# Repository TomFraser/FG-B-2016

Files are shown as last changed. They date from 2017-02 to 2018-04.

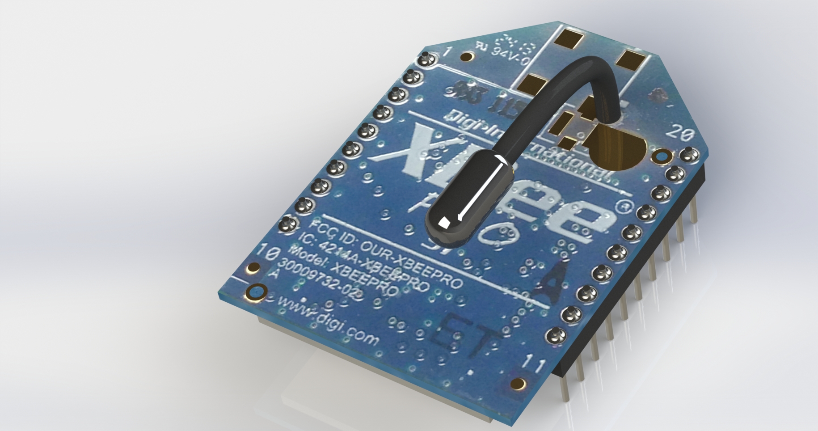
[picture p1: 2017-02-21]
design/components/xBee/Renderings/XBeeRender2.JPG

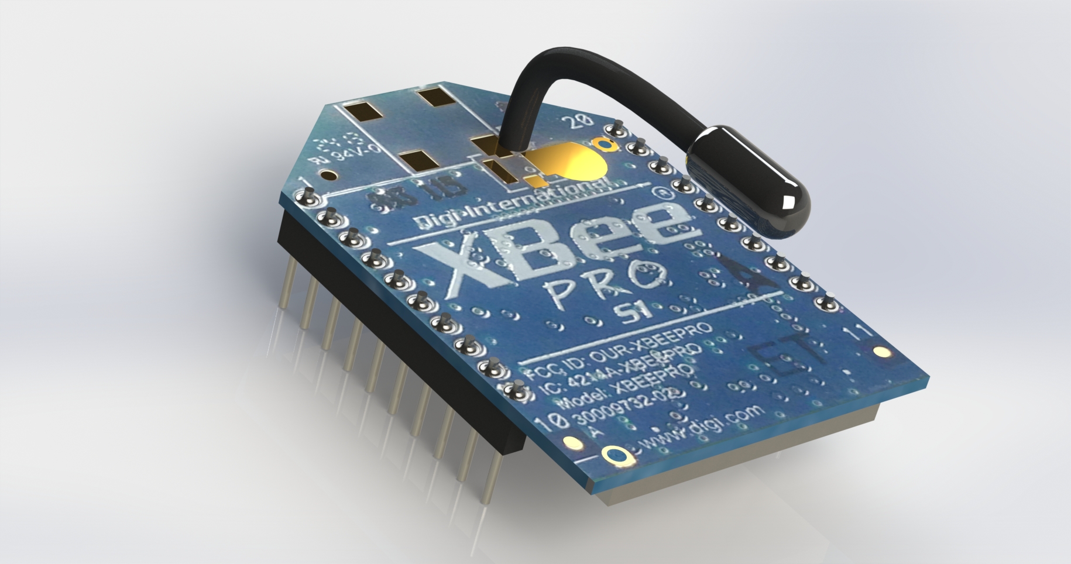
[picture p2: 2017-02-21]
design/components/xBee/Renderings/XBeeRender1.JPG

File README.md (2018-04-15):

# FG&B 2016 Repo
-------------------------------------------------------------

**Feel Free To Use Any Concepts Used Within This Repo.**
**If You Plan On Copying Large Parts Of Code, Please Email tr.fraser@bigpond.com For Permission**

-------------------------------------------------------------

**SHF Robotics**

Main Repo for FG&B Robotics (Formerly SHF Robotics) 2016

Tom Hulbert, Tom Fraser, Alistair English, William Plummer, Cooper Richmond :heart::heart:

-------------------------------------------------------------

To Do List
- [x] Make Robot
- [x] Make Robot Work
- [x] Watch Robot Fail at Nationals Because of the **curse**
- ^^^^ IT REALLY HAPPENED!

-------------------------------------------------------------

Sorry about rude commit messages, comments and messy code.

-------------------------------------------------------------

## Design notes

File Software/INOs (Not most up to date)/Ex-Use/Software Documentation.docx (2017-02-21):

5 Guys and a Box Robotics

Robot #2 Software Development Documentation

By Thomas Fraser

This documentation explains the ideas and methods used in the programming and design of Robot #2 for 5 Guys and a Box Robotics. The robot in question contains 3 Teensy 3.2 microcontrollers and multiple sensors. To learn more on the sensors used please refer to Hardware development documentation for Robot #2. Each Teensy is in charge of controlling certain sensors. The three Teensies communicate via SPI (Serial Peripheral Interface) to communicate.

Teensy 1:

Teensy one contains the lowest load during running with minimal tasks. Its primary task includes controlling the Serial Clock for the SPI communication, therefore it being the master in the SPI loop as well as communicating with the pixy and interfacing with the touch capacitive display.

Teensy 1 Software Design:

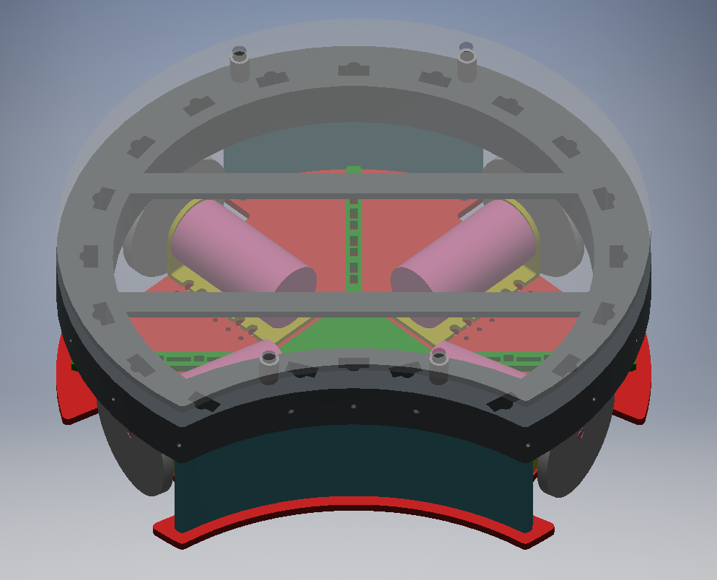
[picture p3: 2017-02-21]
images/renders/robot-front-angle.PNG

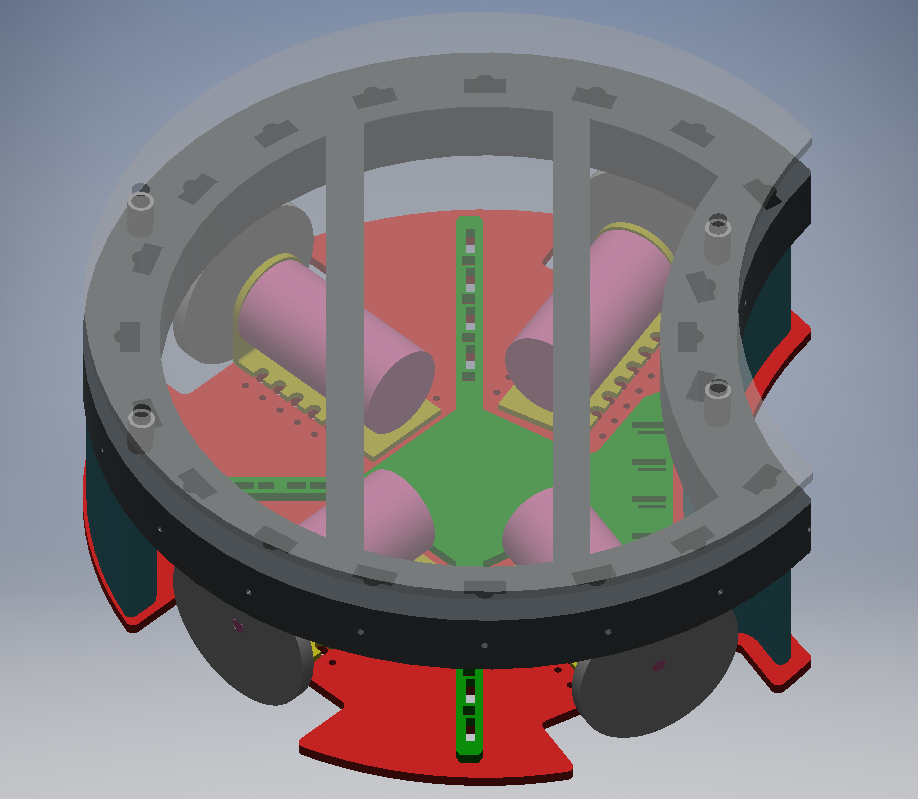
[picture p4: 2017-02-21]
images/renders/robot-side-angle.PNG

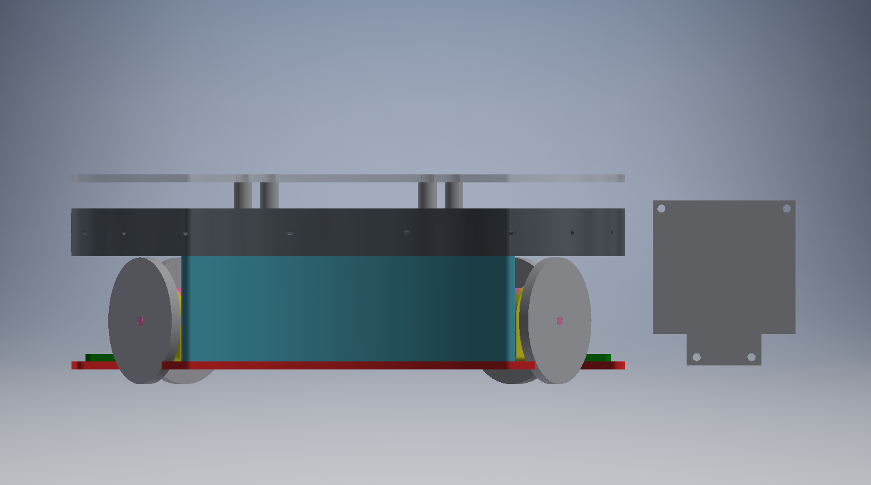
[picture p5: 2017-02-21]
images/renders/robot vs pixy.PNG

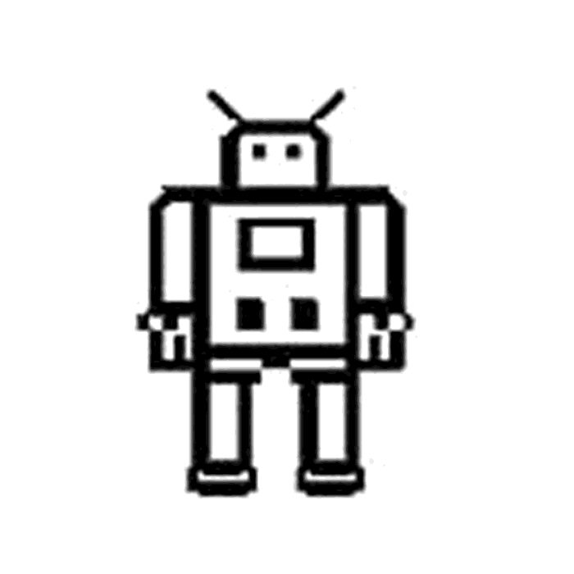
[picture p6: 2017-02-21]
images/stuff/robot.bmp

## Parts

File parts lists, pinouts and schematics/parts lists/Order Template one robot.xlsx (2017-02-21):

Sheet: ORDERS
Date Submitted | Team | Item | Description | Supplier | Vendor PN | Total QTY (inc. spares) | Spares | Price in original currency | Currency | Total price (AUD) | Link | Notes
2016-02-09 | SHF | LED | White L.E.D | Lighthouse LEDs |  | 25 |  | $0.26 | AUD | $6.50 | http://lighthouseleds.com/0805-smd-led-white-ultra-bright-340-mcd.html
2016-02-09 | SHF | LED | Red L.E.D | Lighthouse LEDs |  | 25 |  | $0.26 | AUD | $6.50 | http://lighthouseleds.com/0805-smd-led-red-ultra-bright-170-mcd.html
2016-02-09 | SHF | RES | 100 Ohm Resistor | Digi-Key |  | 50 |  | $0.06 | AUD | $2.94 | http://www.digikey.com.au/product-detail/en/CRCW0805100RJNEA/541-100ACT-ND/1180316
2016-02-09 | SHF | RES | 60 Ohm Resistor | Digi-Key |  | 25 |  | $0.14 | AUD | $3.50 | http://www.digikey.com.au/product-detail/en/RC0805FR-0760R4L/311-60.4CRCT-ND/731020
2016-02-09 | SHF | TRMPOT | Trim Pot 2k Ohm | Digi-Key |  | 5 |  | $1.48 | AUD | $7.40 | http://www.digikey.com.au/product-detail/en/3361P-1-202GLF/3361P-202GLFCT-ND/1089398
2016-02-09 | SHF | CAP | 100 (22) uF Cap | Digi-Key |  | 10 |  | $0.42 | AUD | $4.19 | http://www.digikey.com.au/product-detail/en/GRM21BR61E226ME44L/490-10749-1-ND/5251351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
2016-02-09 | SHF | CAP | 10 uF Cap | Digi-Key |  | 10 |  | $0.23 | AUD | $2.26 | http://www.digikey.com.au/product-detail/en/GRM21BR61E106KA73L/490-5523-1-ND/2334919
2016-02-09 | SHF | CAP | 1000uF Cap | Digi-Key |  | 10 |  | $0.92 | AUD | $9.20 | http://www.digikey.com.au/product-detail/en/UVR1V102MHD/493-1085-ND/588826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
2016-02-09 | SHF | VREG | 3.3v Vreg LM1084 | Digi-Key |  | 3 |  | $4.29 | AUD | $12.87 | http://www.digikey.com.au/product-detail/en/LM1084IS-3.3%2FNOPB/LM1084IS-3.3%2FNOPB-ND/363551
2016-02-09 | SHF | VREG | 5v Vreg LM1084 | Digi-Key |  | 3 |  | $4.29 | AUD | $12.87 | http://www.digikey.com.au/product-detail/en/LM1084IS-5.0%2FNOPB/LM1084IS-5.0%2FNOPB-ND/363552
2016-02-09 | SHF | OTHER | Screw Terminal 5mm (10pcs) | Digi-Key |  | 5 |  | $1.89 | AUD | $9.45 | http://www.ebay.com.au/itm/10Pcs-300V-2-Pin-Screw-Terminal-Block-Connector-5mm-Pitch-Panel-PCB-Mount-K2301-/351023553144
2016-02-09 | SHF | FUSE | Blade Fuse Holder | Digi-Key |  | 4 |  | $4.90 | AUD | $19.60 | http://www.digikey.com.au/product-detail/en/01530007Z/F064-ND/183333
2016-02-09 | SHF | FUSE | Blade Fuse 2 amp | Digi-Key |  | 5 |  | $1.52 | AUD | $7.60 | http://www.digikey.com.au/product-detail/en/BK%2FATM-2/283-2323-ND/264844
2016-02-09 | SHF | FUSE | Blade Fuses 7.5 amp | Digi-Key |  | 5 |  | $1.52 | AUD | $7.60 | http://www.digikey.com.au/product-detail/en/BK%2FATM-7-1%2F2/283-2327-ND/264851
2016-02-09 | SHF | JUMPR | JST Connectors | Digi-Key |  | 10 |  | $0.75 | AUD | $7.50 | http://www.digikey.com.au/product-detail/en/B2B-PH-SM4-TB(LF)(SN)/455-1734-1-ND/926831
2016-02-09 | SHF | JUMPR | JST Connector Receptical | Digi-Key |  | 15 |  | $0.14 | AUD | $2.10 | http://www.digikey.com.au/product-detail/en/PHR-2/455-1165-ND/608607
2016-02-09 | SHF | JUMPR | JST Crimp | Digi-Key |  | 25 |  | $0.14 | AUD | $3.50 | http://www.digikey.com.au/product-detail/en/SPH-002T-P0.5S/455-1127-1-ND/527358
2016-02-09 | SHF | JUMPR | 2x10 Shrouded Header Receptical | Ebay |  | 1 |  | $5.39 | AUD | $5.39 | http://www.ebay.com.au/itm/10-Pcs-2-54mm-2x10-Pin-20-Pin-Straight-Male-Shrouded-PCB-Box-header-IDC-Socket-/181148921363
2016-02-09 | SHF | JUMPR | 2x10 Shrouded Header Housing | Ebay |  | 1 |  | $7.10 | AUD | $7.10 | http://www.ebay.com.au/itm/10-Pcs-2-54mm-2x10-Pin-20-Pin-Male-Header-IDC-Ribbon-Cable-Transition-Connector-/171035372041
2016-02-09 | SHF | JUMPR | Ribbon Cable | Ebay |  | 1 |  | $13.86 | AUD | $13.86 | http://www.ebay.com.au/itm/6M-20-Pin-IDE-PATA-Extension-Flat-Ribbon-Cable-Wire-Gray-/331683344969
2016-02-09 | SHF | OTHER | Photo Transistor TEMT6000 | Allied Electronics |  | 25 |  | $0.63 | AUD | $15.75 | http://www.alliedelec.com/siliconix-vishay-temt6000x01/70026423/
2016-02-09 | SHF | OTHER | TSOPS | Tris10 |  | 0.5 |  | $60.00 | AUD | $30.00 | https://tris10.com/product/ir-sensor-50
2016-02-09 | SHF | MOTOR | Toshiba Motor Controller | Digi-Key |  | 5 |  | $3.72 | AUD | $18.60 | http://www.digikey.com.au/product-detail/en/TB6549PG(O)/TB6549PGO-ND/1730048
2016-02-09 | SHF | CAP | 0.22 uF Ceramic Cap | Digi-Key |  | 25 |  | $0.20 | AUD | $5.00 | http://www.digikey.com.au/product-detail/en/C0805C224K5RACTU/399-3491-1-ND/754784
2016-02-09 | SHF | CAP | 0.01 uF Ceramic (10000pF) Cap | Digi-Key |  | 25 |  | $0.05 | AUD | $1.24 | http://www.digikey.com.au/product-detail/en/GRM216R71H103KA01D/490-1664-1-ND/587472
2016-02-09 | SHF | CAP | 0.1 uF Ceramic Cap | Digi-Key |  | 25 |  | $0.03 | AUD | $0.78 | http://www.digikey.com.au/product-detail/en/CL21F104ZBCNNNC/1276-1007-1-ND/3889093
2016-02-09 | SHF | OTHER | Teensy 3.2 | OSHPark |  | 5 |  | $23.60 | AUD | $118.00 | http://store.oshpark.com/products/teensy-3-1
2016-02-09 | SHF | OTHER | BSS138 (Logic Level) | Digi-Key |  | 15 |  | $0.33 | AUD | $4.95 | http://www.digikey.com.au/product-detail/en/BSS138/BSS138CT-ND/244294
2016-02-09 | SHF | RES | 10k Ohm Resistor | Digi-Key |  | 100 |  | $0.01 | AUD | $1.04 | http://www.digikey.com.au/product-detail/en/RC0805JR-0710KL/311-10KARCT-ND/731188
2016-02-09 | SHF | OTHER | xBee Pro Series 2 | Little Bird |  | 0 |  | $36.65 | AUD | $0.00 | http://littlebirdelectronics.com.au/products/xbee-2mw-wire-antenna-series-2-zigbee-mesh
2016-02-09 | SHF | RES | 4.7k Ohm Resistor | Digi-Key |  | 30 |  | $0.14 | AUD | $4.20 | http://www.digikey.com.au/product-detail/en/RC0805FR-074K7L/311-4.70KCRCT-ND/730876
2016-02-09 | SHF | JUMPR | 2x3 Shrouded Header Receptical | Digi-Key |  | 10 |  | $0.66 | AUD | $6.62 | http://www.digikey.com/product-detail/en/75869-131LF/609-2845-ND/1302569
2016-02-09 | SHF | SENSOR | MPU 9250 | Little Bird |  | 5 |  | $2.92 | AUD | $14.60 | http://www.ebay.com.au/itm/New-SPI-IIC-MPU-9250-9-Axis-Attitude-Sensor-Module-Gyro-Accelerator-Magnetometer-/191152604672
2016-02-09 | SHF | SENSOR | Pixy | Tribotix |  | 1 |  | $70.00 | AUD | $70.00 | http://www.tribotix.com/Products/CharmedLabs/Pixy.htm
2016-02-09 | SHF | LIPO | 14.8v Lipo 1800mAh | Hobby King |  | 3 |  | $22.91 | AUD | $68.73 | http://www.hobbyking.com/hobbyking/store/uh_viewitem.asp?idproduct=24616
2016-02-09 | SHF | LIPO | Lipo Charger (for simultaneous charging) | Hobby King |  | 0 |  | $59.99 | AUD | $0.00 | http://www.hobbyking.com/hobbyking/store/__58285__IMAX_B6AC_V2_Professional_Balance_Charger_Discharger.html
2016-02-09 | SHF | LCD | LCD 2.8" Cap Touch | Adafruit |  | 1 |  | $55.00 | AUD | $55.00 | https://www.adafruit.com/products/2090
2016-02-09 | SHF | OTHER | Switch SPDT | Ali Express |  | 3 |  | $3.55 | AUD | $10.65 | http://www.aliexpress.com/item/SB-DC-12V-20A-Lgnition-LED-SPST-ON-OFF-Car-Toggle-Covered-Rocket-Missile-Switch-Red/32458116746.html
2016-02-09 | SHF | MOTOR | DIP 16 Socket | Digi-Key |  | 5 |  | $0.36 | AUD | $1.80 | http://www.digikey.com.au/product-detail/en/A16-LC-TT/AE9992-ND/821746
2016-02-09 | SHF | OTHER | Hookup Wire | Little Bird |  | 0 |  | $31.05 | AUD | $0.00 | http://littlebirdelectronics.com.au/products/hook-up-wire-spool-set-22awg-solid-core-6-x-25-ft
2016-02-09 | SHF | MOTOR | Motors 500RPM 12V DC | Polulu |  | 5 |  | $12.17 | AUD | $60.85 | http://www.aliexpress.com/item/DC-12V-500RPM-25GA-40mA-High-Torque-Electric-Gear-Box-Motor-25MM/32270478250.html
2016-02-09 | SHF | SOLDER | Solder Paste No Clean Lead-Free | Digi-Key |  | 1 |  | $21.73 | AUD | $21.73 | http://www.digikey.com.au/product-detail/en/SMD291SNL/SMD291SNL-ND/1160001
2016-02-09 | SHF | JUMPR | Male SMD Header 0.1" | Ebay |  | 2 |  | $7.09 | AUD | $14.18 | http://www.ebay.com.au/itm/10pcs-RoHS-2-54mm-Pitch-2X40-Pin-Header-Strip-Double-Row-SMT-SMD-Male-PCB-Board-/271556499758
2016-02-09 | SHF | JUMPR | Female Header 0.1" | Ebay |  | 5 |  | $1.60 | AUD | $8.00 | http://www.ebay.com.au/itm/10pcs-40-Way-Single-Female-HEADER-Connector-0-1-2-54mm-Breakable-Pin-For-PCB-/271841180849
2016-02-09 | SHF | SOLDER | Solder 0.51mm Lead-Free | Digi-Key |  | 0 |  | $30.89 | AUD | $0.00 | http://www.digikey.com.au/product-detail/en/SMDSWLF.020%204OZ/SMDSWLF.020%204OZ-ND/2177058
2016-02-09 | SHF | MOTOR | Dodgy Uranium (Iranium) Omni-Wheels | Alibaba |  | 5 |  | $17.50 | AUD | $87.50 | http://www.alibaba.com/product-detail/omni-directional-wheel_146767461.html
2016-02-09 | SHF | MOTOR | Motor Mounts | Polulu |  | 5 |  | $7.45 | AUD | $37.25 | https://www.pololu.com/product/2676
2016-02-09 | SHF | TRMPOT | Trim Pot 1k Ohm | Digi-Key |  | 10 |  | $1.48 | AUD | $14.80 | http://www.digikey.com.au/product-detail/en/3361P-1-102GLF/3361P-102GLFCT-ND/1089394
2016-02-09 | SHF | RES | 10 Ohm Resistor | Digi-Key |  | 100 |  | $0.01 | AUD | $1.21 | http://www.digikey.com.au/product-detail/en/RC0805FR-0710RL/311-10.0CRCT-ND/730481
2016-02-09 | SHF | JUMPR | XT60 Connector | Hobby King |  | 1 |  | $5.75 | AUD | $5.75 | http://www.hobbyking.com/hobbyking/store/uh_viewitem.asp?idproduct=43416
2016-02-09 | SHF | OTHER | Rocker Switch SPDT (4pcs) | Ebay |  | 3 |  | $1.82 | AUD | $5.46 | http://www.ebay.com.au/itm/4-Pcs-x-AC-250V-6A-125V-10A-on-on-SPDT-Boat-Rocker-Switch-3-Solder-Lug-Pin-Black-/391159131408
2016-02-09 | SHF | SENSOR | M12 130 degree Lense (pixy) | M12Lense.com |  | 1 |  | $9.98 | AUD | $9.98 | http://www.m12lenses.com/2-5mm-F2-5-Board-Lens-p/pt-02520.htm
2016-02-09 | SHF | OTHER | Adhesive Paper | Ebay |  | 1 |  | $2.00 | AUD | $2.00 | http://www.ebay.com.au/itm/20-sheets-A4-105GSM-Inkjet-and-laser-Matte-Label-Paper-Sticker-Adhesive-/181989139085
2016-02-09 | SHF | OTHER | PVC Sheet Grey (at least 1000*300mm) | Plastic Wholesale |  | N/A |  | N/A | AUD |  | http://www.plasticwholesale.com.au/
2016-02-09 | SHF | OTHER | PVC Sheet Clear (at least 1000*300mm) | Plastic Wholesale |  | N/A |  | N/A | AUD |  | http://www.plasticwholesale.com.au/
2016-02-09 | SHF | OTHER | Solid Core Wire 6x25ft | Little Bird |  | 1 |  | $31.00 | AUD | $31.00 | http://littlebirdelectronics.com.au/products/hook-up-wire-spool-set-22awg-solid-core-6-x-25-ft
2016-02-09 | SHF | OTHER | Heat Shrink | Ebay |  | 1 |  | $13.50 | AUD | $13.50 | http://www.ebay.com.au/itm/355pcs-11-Size-Black-Heat-Shrink-Tube-Sleeving-Wrap-Wire-Kit-2-1-/301598776468
2016-02-09 | SHF | OTHER | Braided Cable Sleeve | Ebay |  | 1 |  | $6.00 | AUD | $6.00 | http://www.ebay.com.au/itm/3mm-Black-Expandable-Braided-DENSE-Cable-Sleeve-Cover-x5m-/251251698077
2016-02-09 | SHF | PCB | Top PCB (includes shipping) | Kiki PCBs |  | 1 |  | $131.12 | AUD | $131.12
2016-02-10 | SHF | PCB | Bottom PCB (includes shipping) | Kiki PCBs |  | 1 |  | $132.26 | AUD | $132.26
 |  |  |  |  |  |  |  |  |  | $1161.48
 |  |  |  |  |  |  |  | Spare Monies |  | $38.52

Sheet: Input Lists
Teams | Divisions | Suppliers | Approval | Trainers
ACW | Gen2 | Little Bird | Approved | Mr Noy
SHF | Lightweight | Digi-key | Pending | Steven
J STAND | Open soccer | Jaycar | Denied | Andrew
BBC 1 | Open rescue | Bunnings |  | Brian
BBC 2 | Shared | Hobby King |  | Rob
BBC 3 |  | AliExpress
Shared |  | OSH Park
 |  | Tris10
 |  | Ebay (Digikey preferred)
 |  | Element14 (Digikey preferred)
 |  | Mouser (Digikey preferred)
 |  | The Room of Requirement
 |  | Tosche Station
 |  | MTA
 |  | Bricklink
 |  | Lego
 |  | Diagon Alley
 |  | Other

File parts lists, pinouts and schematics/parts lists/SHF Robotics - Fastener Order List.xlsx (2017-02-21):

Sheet: Instructions
Rename this file so we know which team you are (e.g. Team Pi - Fastener Order List)
Examples on the next sheet are in light grey like this
Include which type of screw you want (e.g. Cap head, Countersunk, Button head)
There is no need to specify if you need philips or hex, the cheapest type will be puchased
Now list your order in the next sheet -->

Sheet: Order List
Item | Thread | Length | Description | Material | Exact QTY per robot
Screw | M3.5 | 12mm | Countersunk | Steel | 10
Nut | 3/16 |  | Wing | Steel | 4
Nut | 3/16 |  | Lock | Steel | 8
Washer | M3 |  |  | Steel | 15
Rod | 3/16 | 200mm |  | Steel | 4
Spacer |  | Varying lengths | 3.15mm diameter or as close to as possible | Nylon | 8

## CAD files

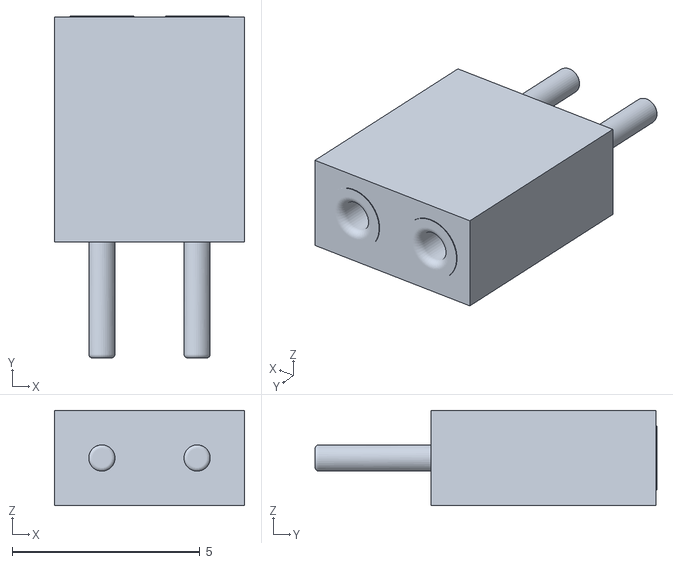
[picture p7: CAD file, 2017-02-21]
design/components/User Library-RM254_2pin.stl
5.08 x 9.12 x 2.54

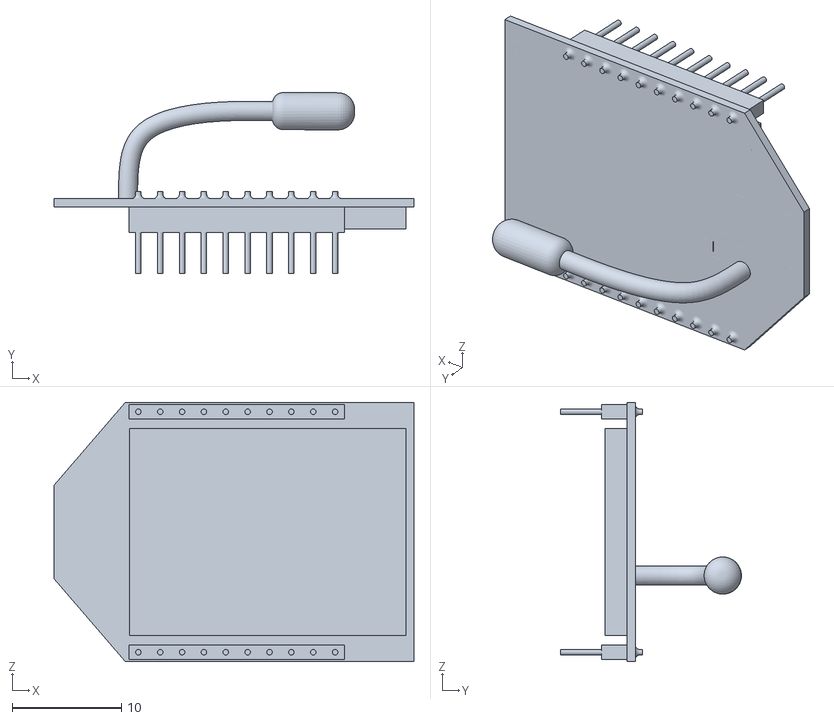
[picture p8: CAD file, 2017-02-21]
design/components/xBee/XBeeProS1.STL
32.9 x 16.6 x 23.7

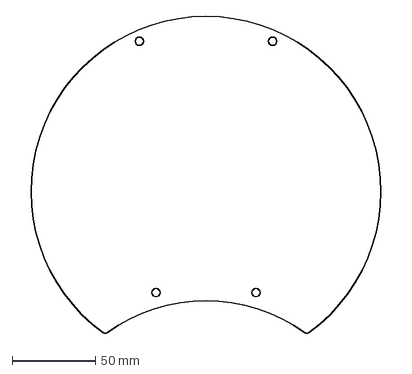
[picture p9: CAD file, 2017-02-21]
design/top plate.dxf
227.8 x 190.5 mm

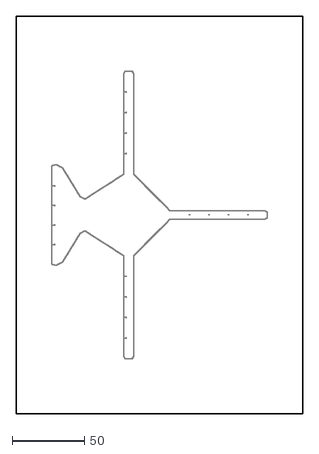
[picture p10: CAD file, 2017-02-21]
eagle/bottom PCB/bottom plate pcb outline-Layout1.dxf
198.4 x 275.4

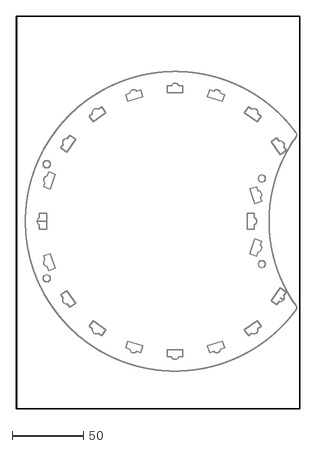
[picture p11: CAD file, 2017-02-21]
eagle/top PCB/TSOP Plate-Layout1.dxf
198.4 x 275.4

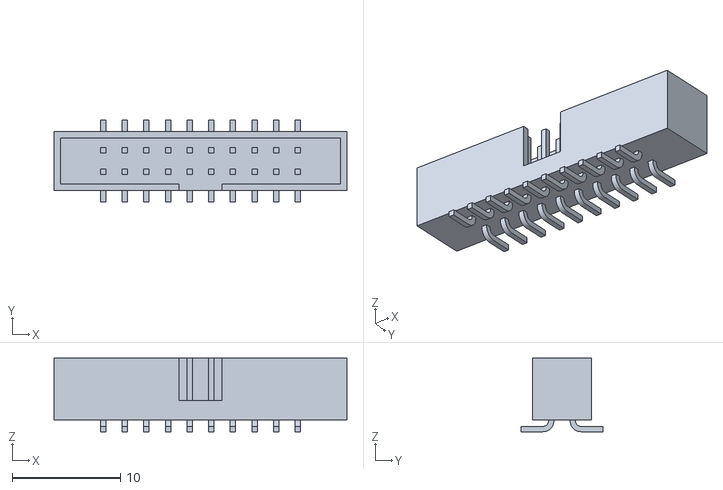
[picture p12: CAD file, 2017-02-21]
design/components/User Library-Toby-20-way_2mm_box_header_C05s_series.stl
27.1 x 7.60 x 6.80

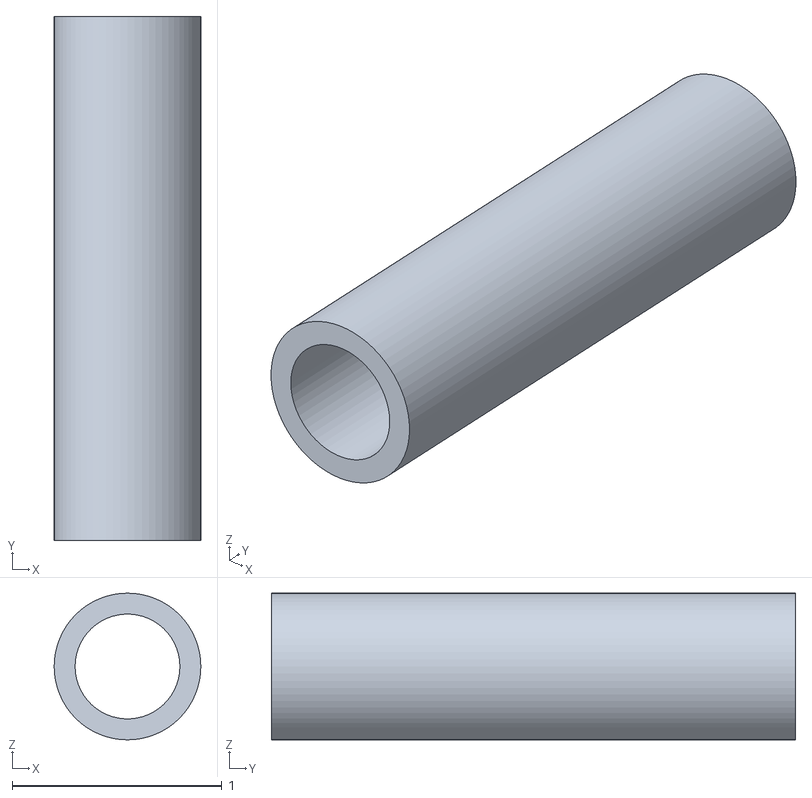
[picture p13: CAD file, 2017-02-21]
design/small spacer.stl
0.7 x 2.50 x 0.7

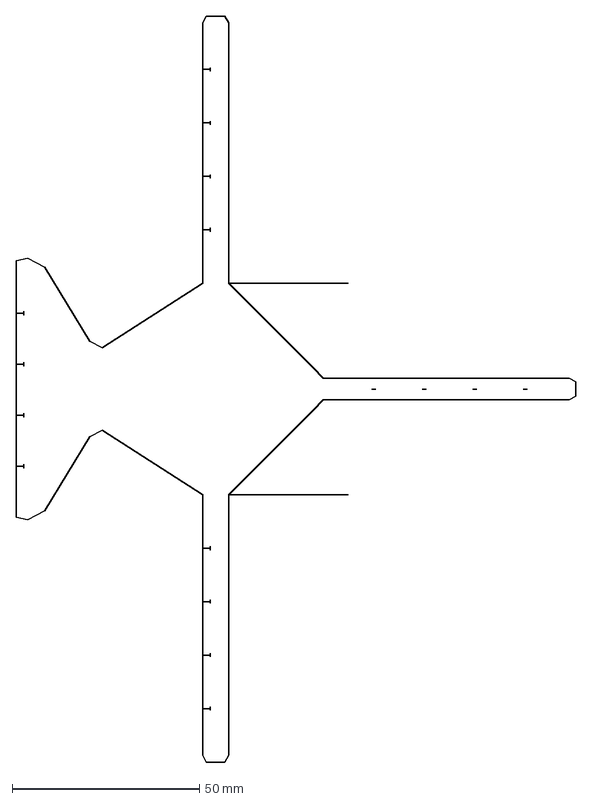
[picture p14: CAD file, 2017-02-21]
eagle/bottom PCB/bottom plate pcb outline.dxf
149.5 x 199.2 mm

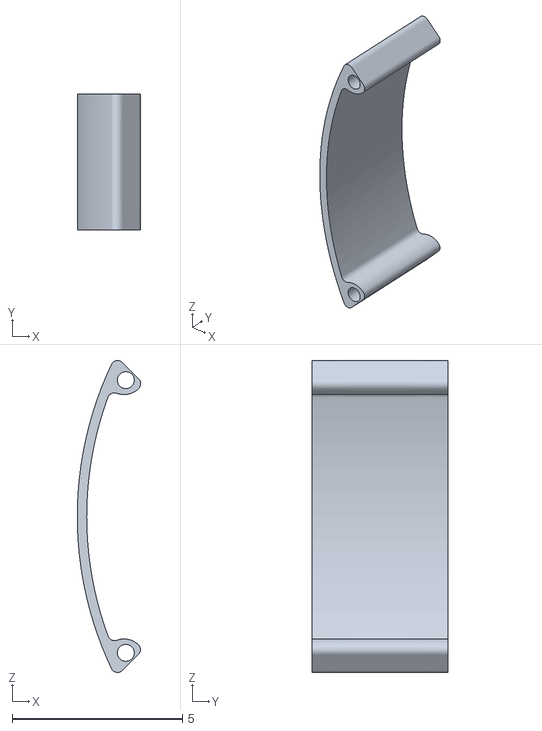
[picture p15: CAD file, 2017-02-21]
design/back plate.stl
1.86 x 4.00 x 9.15

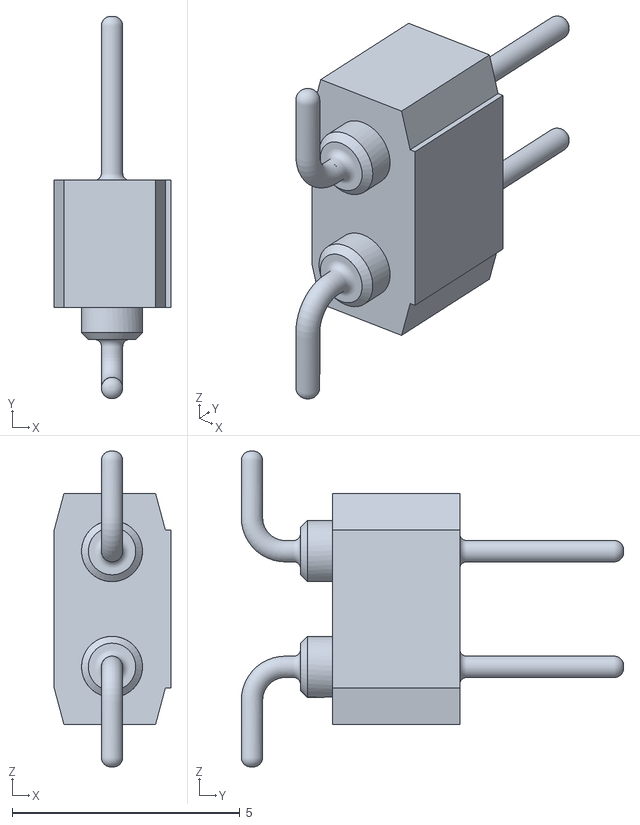
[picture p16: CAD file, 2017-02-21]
design/components/User Library-2mmSMT_1W.stl
2.56 x 8.40 x 6.94

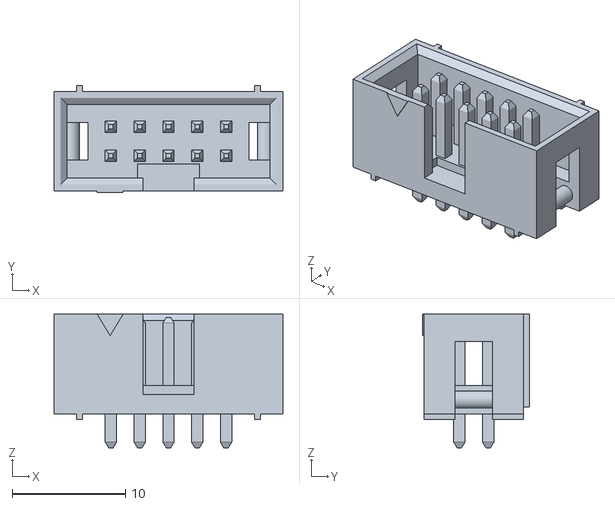
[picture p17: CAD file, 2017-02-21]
design/components/User Library-HDB-10.stl
20.2 x 9.40 x 11.8

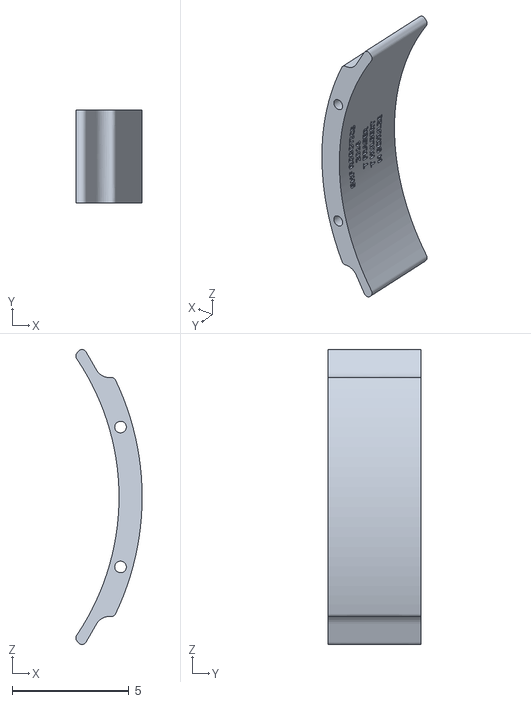
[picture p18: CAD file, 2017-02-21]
design/Goal.stl
2.84 x 4.00 x 12.7

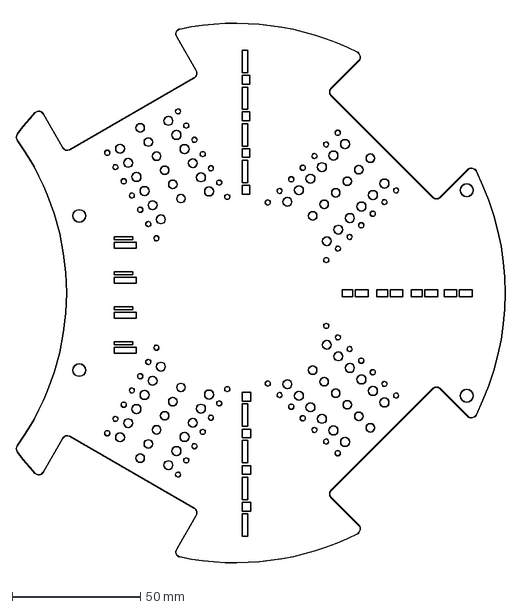
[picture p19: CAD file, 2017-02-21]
design/bottom plate.dxf
194.2 x 215.4 mm

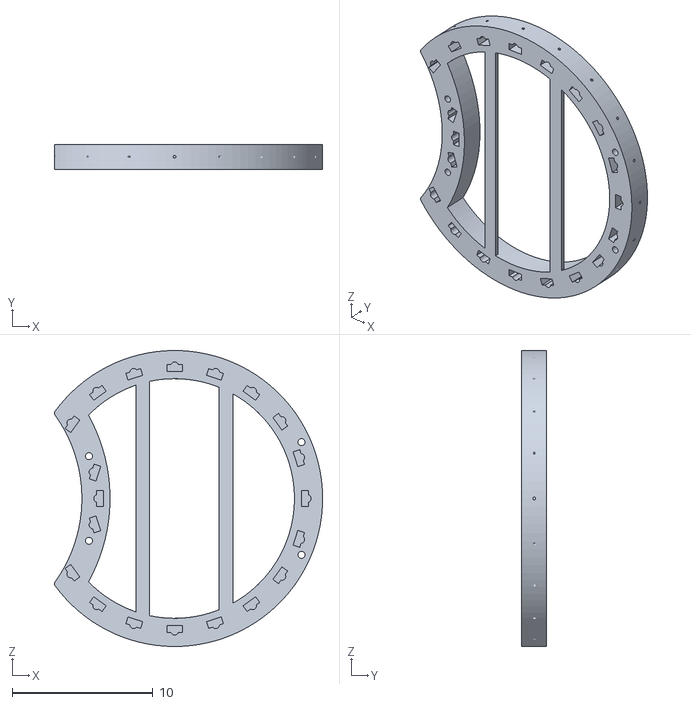
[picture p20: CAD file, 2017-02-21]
design/TSOP Plate.stl
19.0 x 1.80 x 21.0

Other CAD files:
design/Bottom Plate.ipt
design/Goal.ipt
design/Middle plate.ipt
design/OldVersions/Bottom Plate.0031.ipt
design/OldVersions/Goal.0009.ipt
design/OldVersions/Middle plate.0012.ipt
design/OldVersions/Spacer long.0002.ipt
design/OldVersions/Spacer.0001.ipt
design/OldVersions/TSOP Plate.0018.ipt
design/OldVersions/battery gate mirrored.0002.iam
design/OldVersions/battery gate pin.0014.ipt
design/OldVersions/battery gate upper mirrored.0001.ipt
design/OldVersions/battery gate upper.0007.ipt
design/OldVersions/battery gate.0003.ipt
design/OldVersions/battery gate.0009.iam
design/OldVersions/handle.0007.ipt
design/OldVersions/motor mount.0001.ipt
design/OldVersions/motor.0001.ipt
design/OldVersions/pixy mount.0001.ipt
design/OldVersions/pixy.0001.ipt
design/OldVersions/robot with small motors.0026.iam
design/OldVersions/robot.0017.iam
design/OldVersions/small motor mount.0005.ipt
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

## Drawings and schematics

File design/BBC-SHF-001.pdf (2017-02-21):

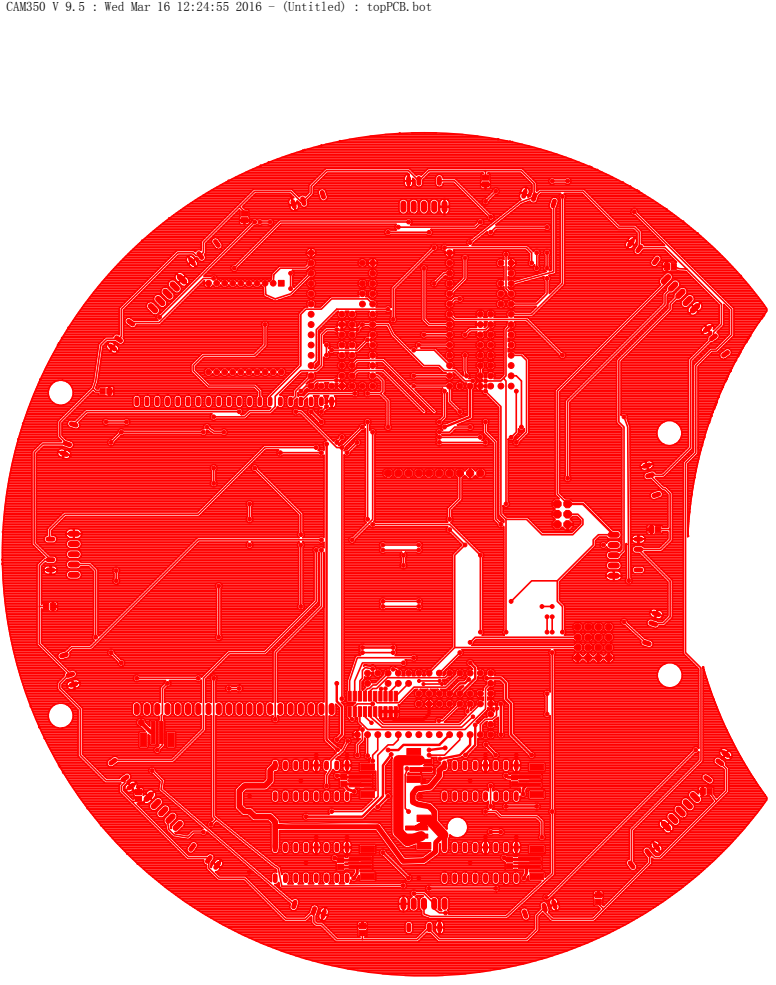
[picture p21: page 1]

CAM350 V 9.5 : Wed Mar 16 12:24:55 2016 - (Untitled) : topPCB.bot

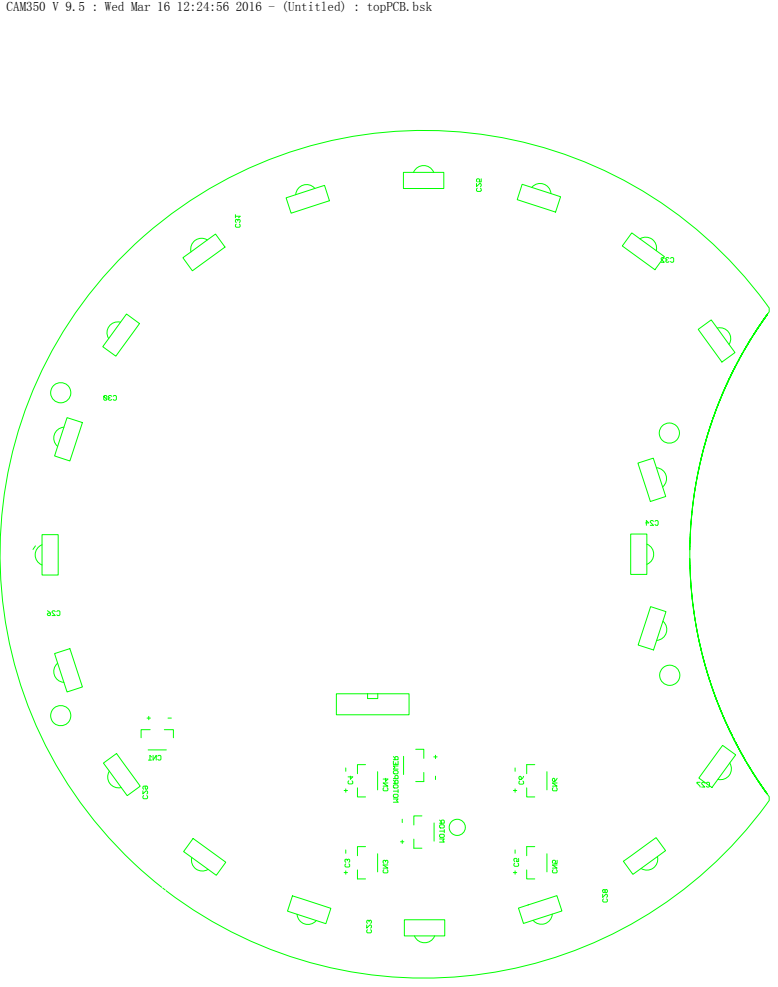
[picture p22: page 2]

CAM350 V 9.5 : Wed Mar 16 12:24:56 2016 - (Untitled) : topPCB.bsk

CAM350 V 9.5 : Wed Mar 16 12:24:56 2016 - (Untitled) : topPCB.bsp

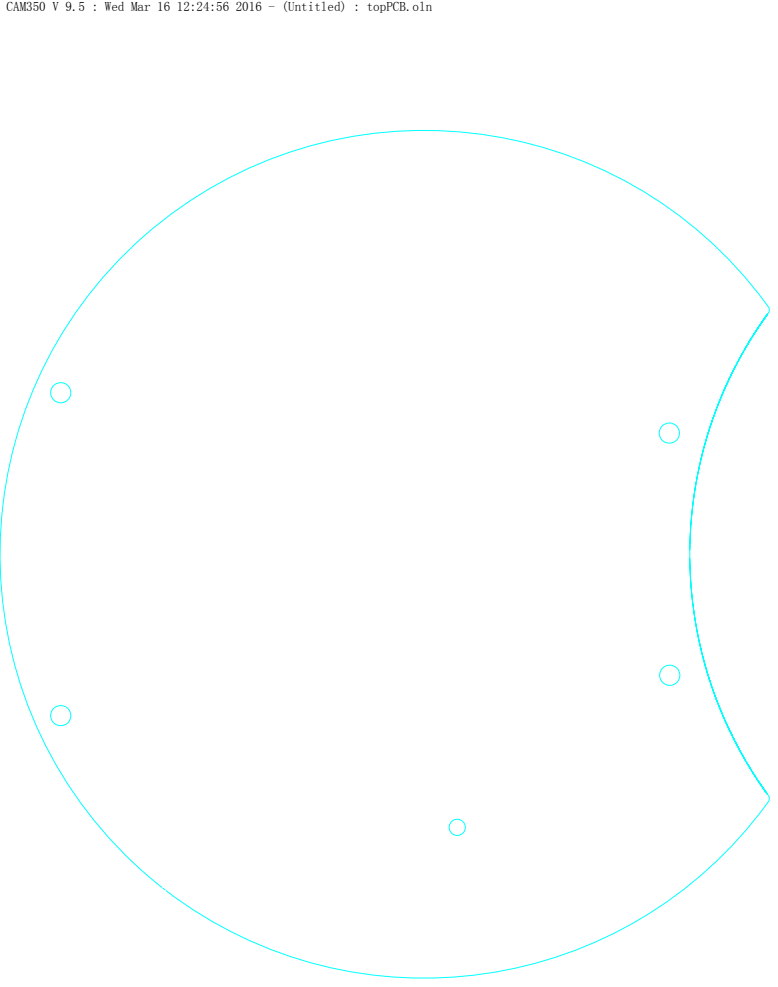
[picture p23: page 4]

CAM350 V 9.5 : Wed Mar 16 12:24:56 2016 - (Untitled) : topPCB.oln

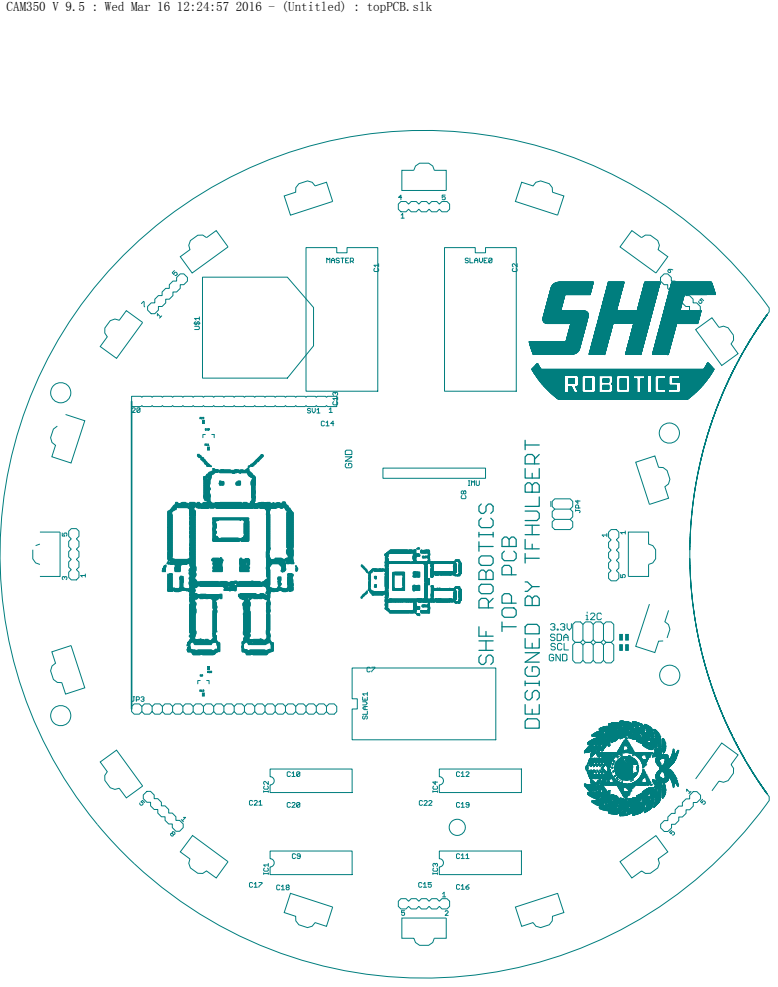
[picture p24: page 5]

CAM350 V 9.5 : Wed Mar 16 12:24:57 2016 - (Untitled) : topPCB.slk

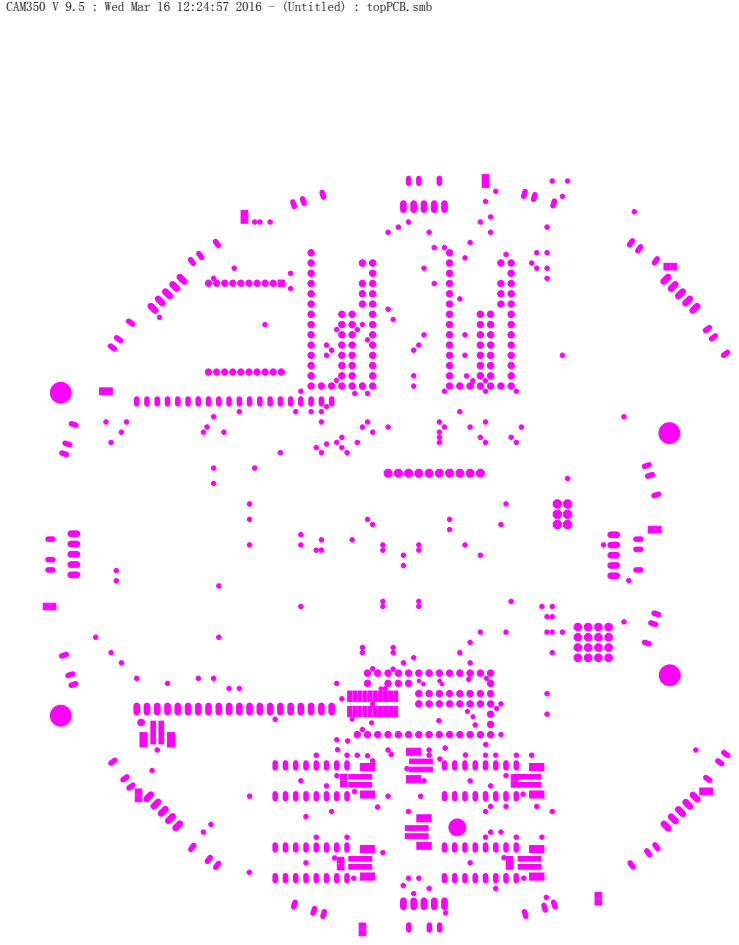
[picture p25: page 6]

CAM350 V 9.5 : Wed Mar 16 12:24:57 2016 - (Untitled) : topPCB.smb

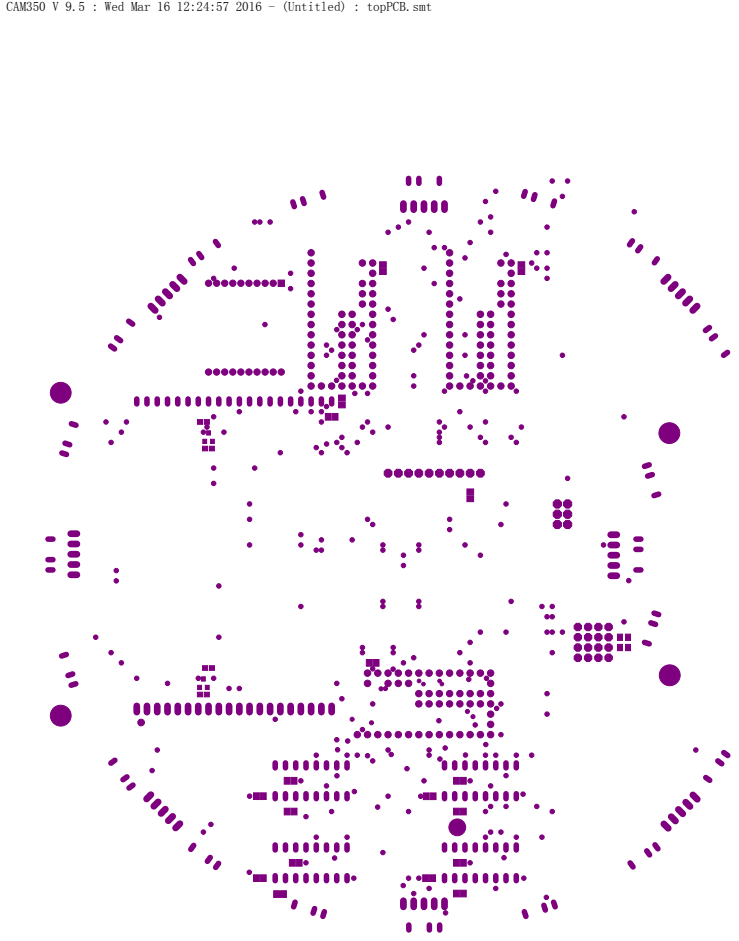
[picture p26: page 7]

CAM350 V 9.5 : Wed Mar 16 12:24:57 2016 - (Untitled) : topPCB.smt

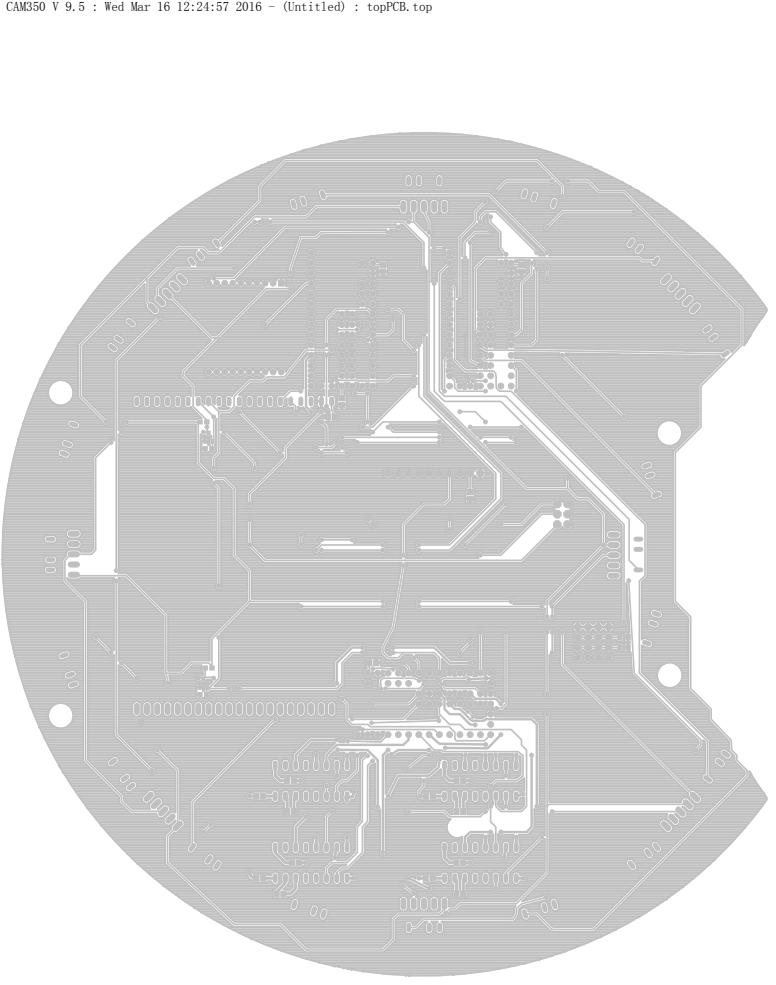
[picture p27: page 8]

CAM350 V 9.5 : Wed Mar 16 12:24:57 2016 - (Untitled) : topPCB.top

CAM350 V 9.5 : Wed Mar 16 12:24:57 2016 - (Untitled) : topPCB.tsp

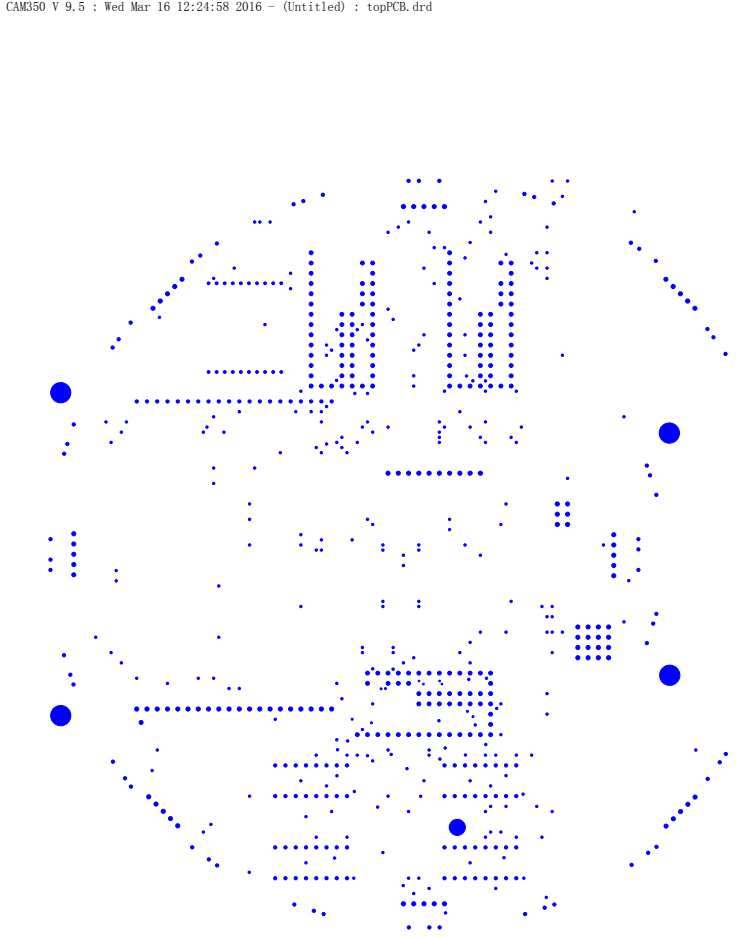
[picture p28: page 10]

CAM350 V 9.5 : Wed Mar 16 12:24:58 2016 - (Untitled) : topPCB.drd

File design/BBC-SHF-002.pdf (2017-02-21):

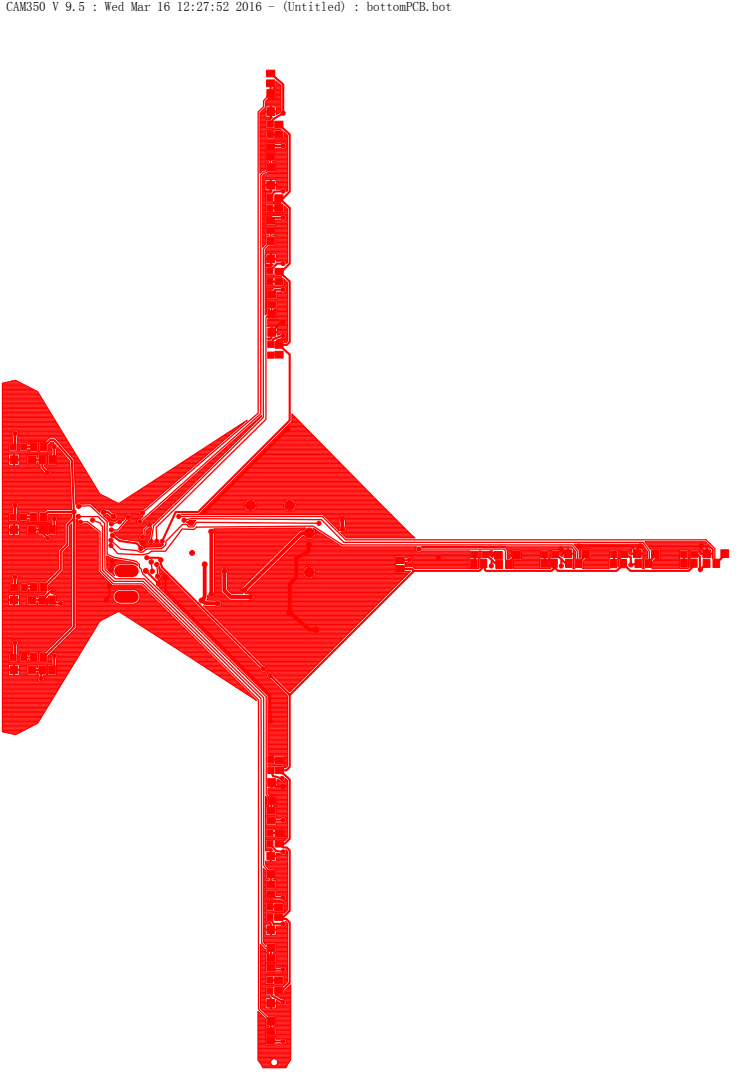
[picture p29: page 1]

CAM350 V 9.5 : Wed Mar 16 12:27:52 2016 - (Untitled) : bottomPCB.bot

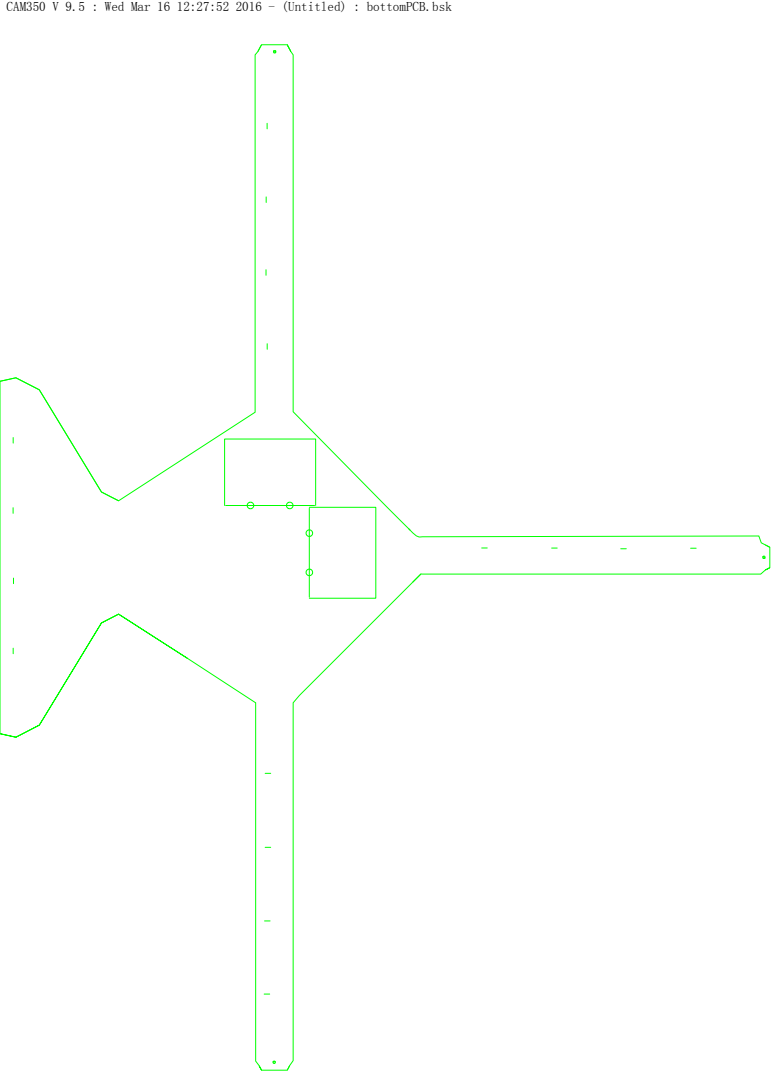
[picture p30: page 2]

CAM350 V 9.5 : Wed Mar 16 12:27:52 2016 - (Untitled) : bottomPCB.bsk

CAM350 V 9.5 : Wed Mar 16 12:27:52 2016 - (Untitled) : bottomPCB.bsp

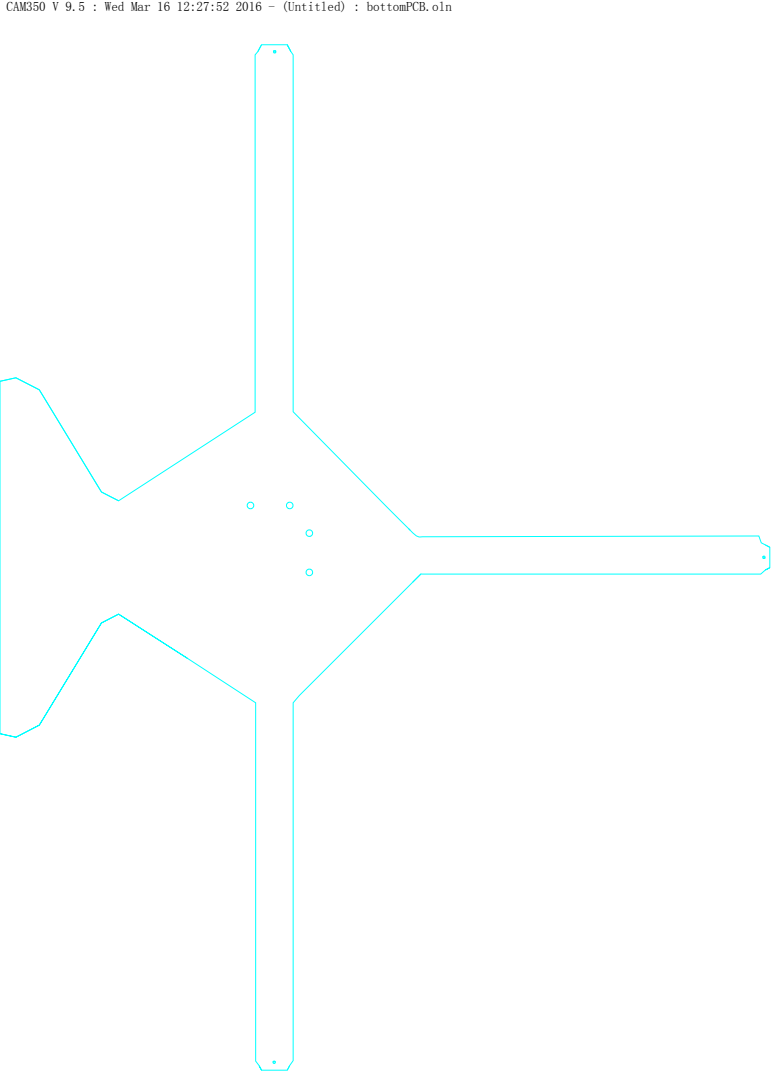
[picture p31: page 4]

CAM350 V 9.5 : Wed Mar 16 12:27:52 2016 - (Untitled) : bottomPCB.oln

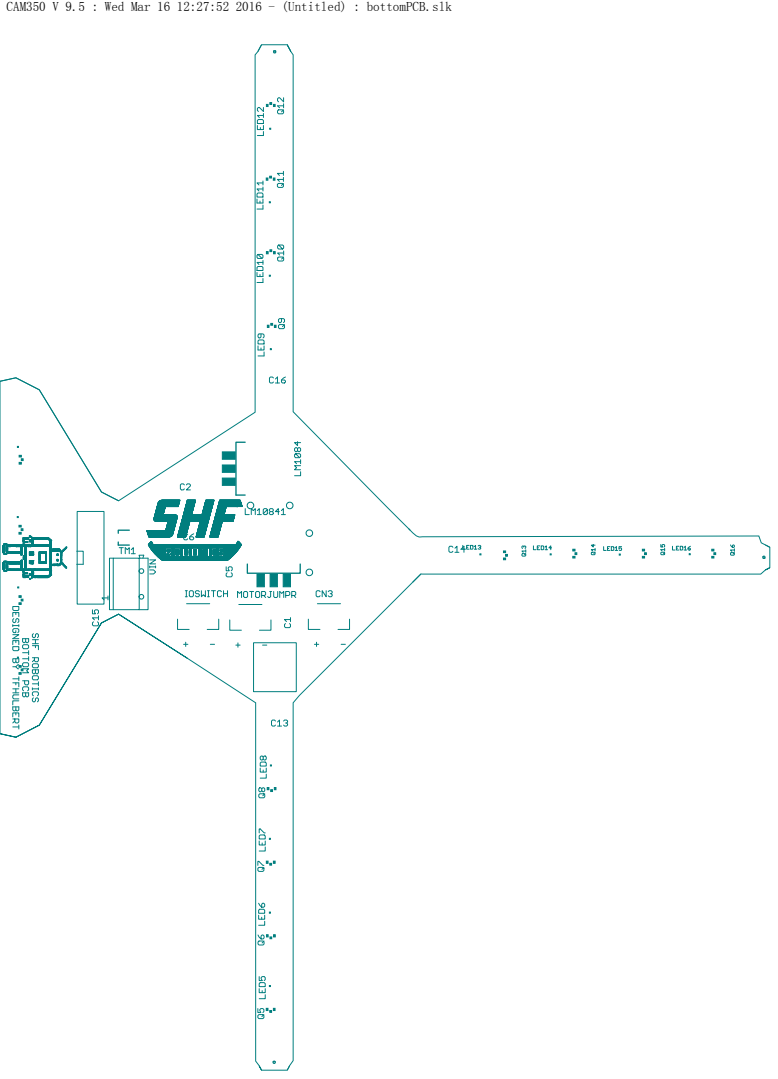
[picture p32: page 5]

CAM350 V 9.5 : Wed Mar 16 12:27:52 2016 - (Untitled) : bottomPCB.slk


CAM350 V 9.5 : Wed Mar 16 12:27:52 2016 - (Untitled) : bottomPCB.smb


CAM350 V 9.5 : Wed Mar 16 12:27:52 2016 - (Untitled) : bottomPCB.smt


CAM350 V 9.5 : Wed Mar 16 12:27:52 2016 - (Untitled) : bottomPCB.top

CAM350 V 9.5 : Wed Mar 16 12:27:52 2016 - (Untitled) : bottomPCB.tsp


CAM350 V 9.5 : Wed Mar 16 12:27:52 2016 - (Untitled) : bottomPCB.drd






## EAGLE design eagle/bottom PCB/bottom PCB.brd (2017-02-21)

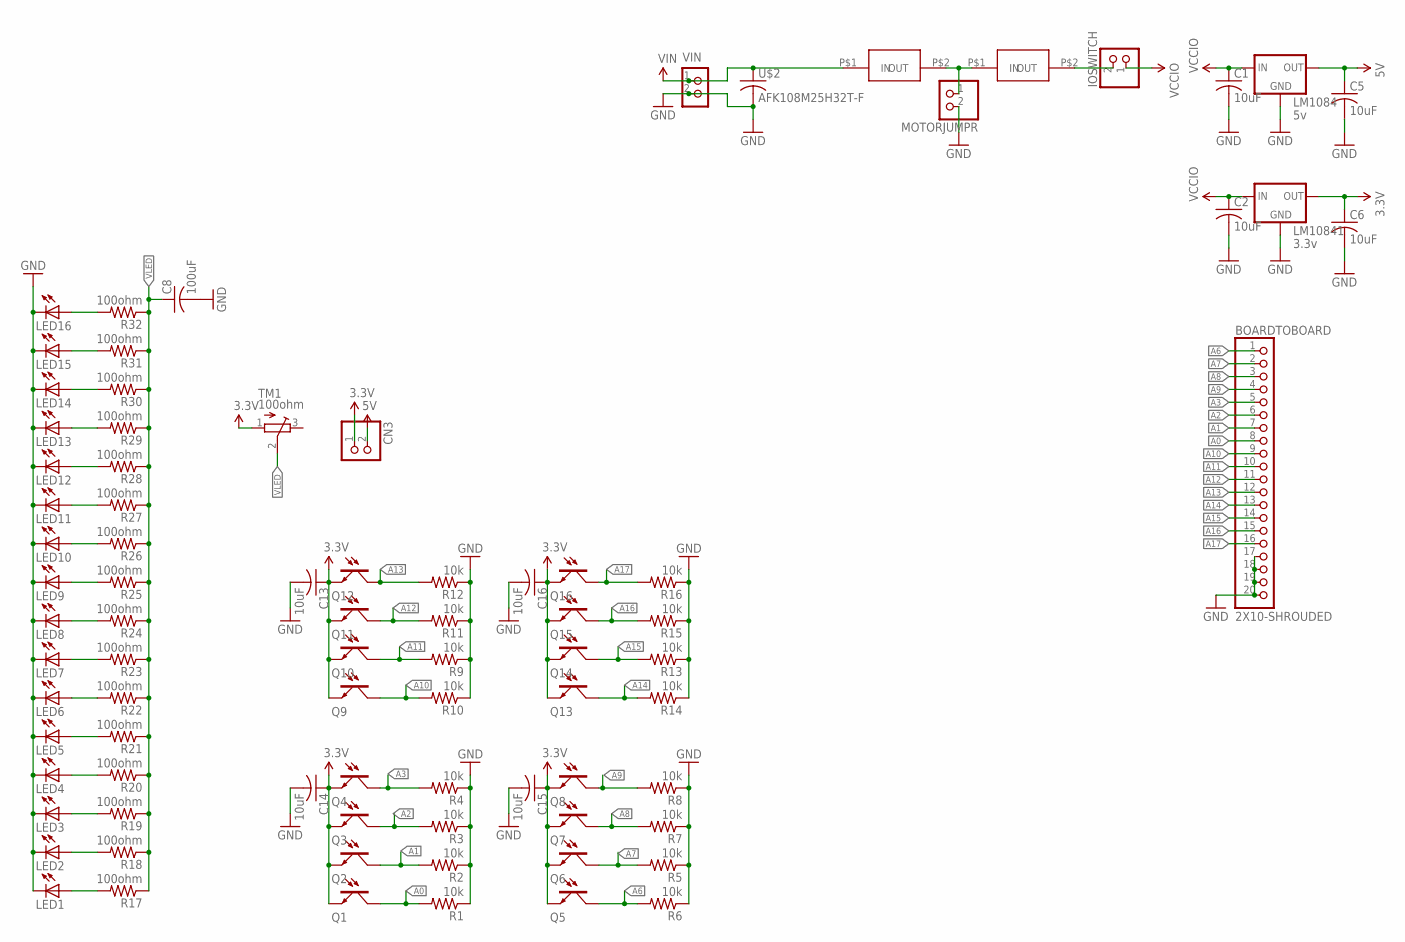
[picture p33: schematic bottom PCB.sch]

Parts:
2A: 0153007_FUSE; 0153007_
5A: 5a; 0153007_
BOARDTOBOARD: 2X10-SHROUDED
C1, C2, C5, C6, C13, C14, C15, C16: 10uF; C0805
C8: 100uF; C0805
CN3: JST_2PIN-SMT; JST-PH-2-SMT
IOSWITCH: JST_2PIN-SMT; JST-PH-2-SMT
LED1, LED2, LED3, LED4, LED5, LED6, LED7, LED8, LED9, LED10, LED11, LED12, LED13, LED14, LED15, LED16: LEDCHIPLED_0805; CHIPLED_0805
LM1084: 5v; D2PACK
LM10841: 3.3v; D2PACK
MOTORJUMPR: JST_2PIN-SMT; JST-PH-2-SMT
Q1, Q2, Q3, Q4, Q5, Q6, Q7, Q8, Q9, Q10, Q11, Q12, Q13, Q14, Q15, Q16: PHOTOTRANSISTORCHIPLED_1206; CHIPLED_1206
R1, R2, R3, R4, R5, R6, R7, R8, R9, R10, R11, R12, R13, R14, R15, R16: 10k; M0805
R17, R18, R19, R20, R21, R22, R23, R24, R25, R26, R27, R28, R29, R30, R31, R32: 100ohm; M0805
TM1: 100ohm; TC33X
U$2: AFK108M25H32T-F
VIN: CON_TERMINAL_BLOCK_02-5MM; TERMINAL_BLOCK_2P_5

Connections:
3.3V: C6.1, C13.1, C14.1, C15.1, C16.1, CN3.1 (2), LM10841.2 (VOUT), Q1.C, Q2.C, Q3.C, Q4.C, Q5.C, Q6.C, Q7.C, Q8.C, Q9.C, Q10.C, Q11.C, Q12.C, Q13.C, Q14.C, Q15.C, Q16.C, TM1.1 (A)
5V: C5.1, CN3.2 (1), LM1084.2 (VOUT)
A0: BOARDTOBOARD.8, Q1.A, R1.2
A1: BOARDTOBOARD.7, Q2.A, R2.2
A2: BOARDTOBOARD.6, Q3.A, R3.2
A3: BOARDTOBOARD.5, Q4.A, R4.2
A6: BOARDTOBOARD.1, Q5.A, R6.2
A7: BOARDTOBOARD.2, Q6.A, R5.2
A8: BOARDTOBOARD.3, Q7.A, R7.2
A9: BOARDTOBOARD.4, Q8.A, R8.2
A10: BOARDTOBOARD.9, Q9.A, R10.2
A11: BOARDTOBOARD.10, Q10.A, R9.2
A12: BOARDTOBOARD.11, Q11.A, R11.2
A13: BOARDTOBOARD.12, Q12.A, R12.2
A14: BOARDTOBOARD.13, Q13.A, R14.2
A15: BOARDTOBOARD.14, Q14.A, R13.2
A16: BOARDTOBOARD.15, Q15.A, R15.2
A17: BOARDTOBOARD.16, Q16.A, R16.2
GND: BOARDTOBOARD.17, BOARDTOBOARD.18, BOARDTOBOARD.19, BOARDTOBOARD.20, C1.2, C2.2, C5.2, C6.2, C8.2, C13.2, C14.2, C15.2, C16.2, LED1.C, LED2.C, LED3.C, LED4.C, LED5.C, LED6.C, LED7.C, LED8.C, LED9.C, LED10.C, LED11.C, LED12.C, LED13.C, LED14.C, LED15.C, LED16.C, LM1084.1 (GND), LM10841.1 (GND), MOTORJUMPR.2 (1), R1.1, R2.1, R3.1, R4.1, R5.1, R6.1, R7.1, R8.1, R9.1, R10.1, R11.1, R12.1, R13.1, R14.1, R15.1, R16.1, U$2.POS (2), VIN.2
unnamed: LED1.A, R17.2
unnamed: 2A.P$2 (OUT), IOSWITCH.2 (1)
unnamed: LED2.A, R18.2
unnamed: LED3.A, R19.2
unnamed: LED4.A, R20.2
unnamed: LED5.A, R21.2
unnamed: LED6.A, R22.2
unnamed: LED7.A, R23.2
unnamed: LED8.A, R24.2
unnamed: LED9.A, R25.2
unnamed: LED10.A, R26.2
unnamed: LED11.A, R27.2
unnamed: LED12.A, R28.2
unnamed: LED13.A, R29.2
unnamed: LED14.A, R30.2
unnamed: LED15.A, R31.2
unnamed: LED16.A, R32.2
VCC: 2A.P$1 (IN), 5A.P$2 (OUT), MOTORJUMPR.1 (2)
VCCIO: C1.1, C2.1, IOSWITCH.1 (2), LM1084.3 (VIN), LM10841.3 (VIN)
VIN: 5A.P$1 (IN), U$2.NEG (1), VIN.1
VLED: C8.1, R17.1, R18.1, R19.1, R20.1, R21.1, R22.1, R23.1, R24.1, R25.1, R26.1, R27.1, R28.1, R29.1, R30.1, R31.1, R32.1, TM1.2 (S)

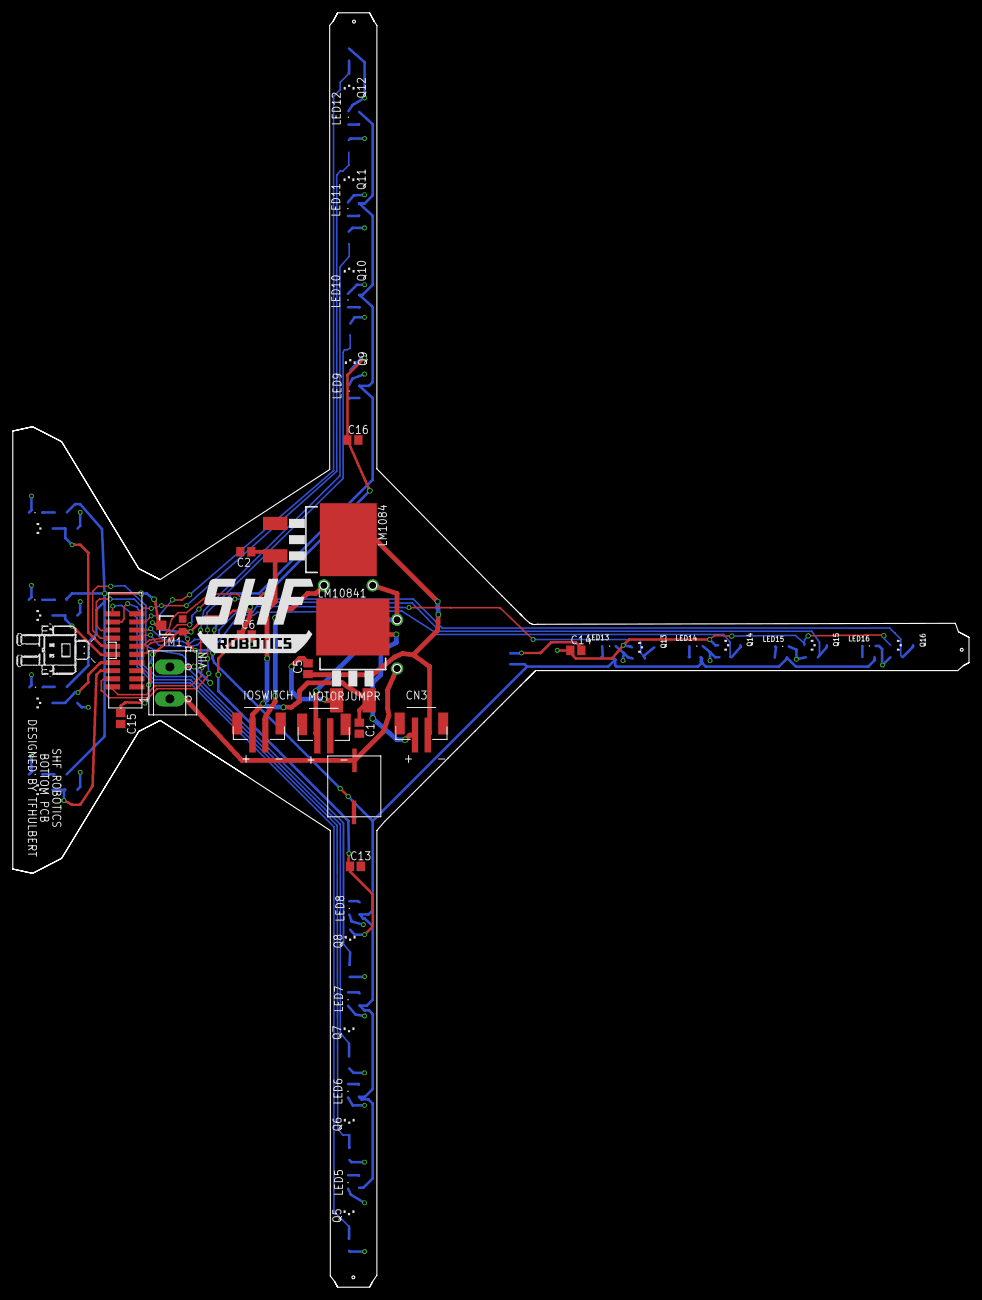
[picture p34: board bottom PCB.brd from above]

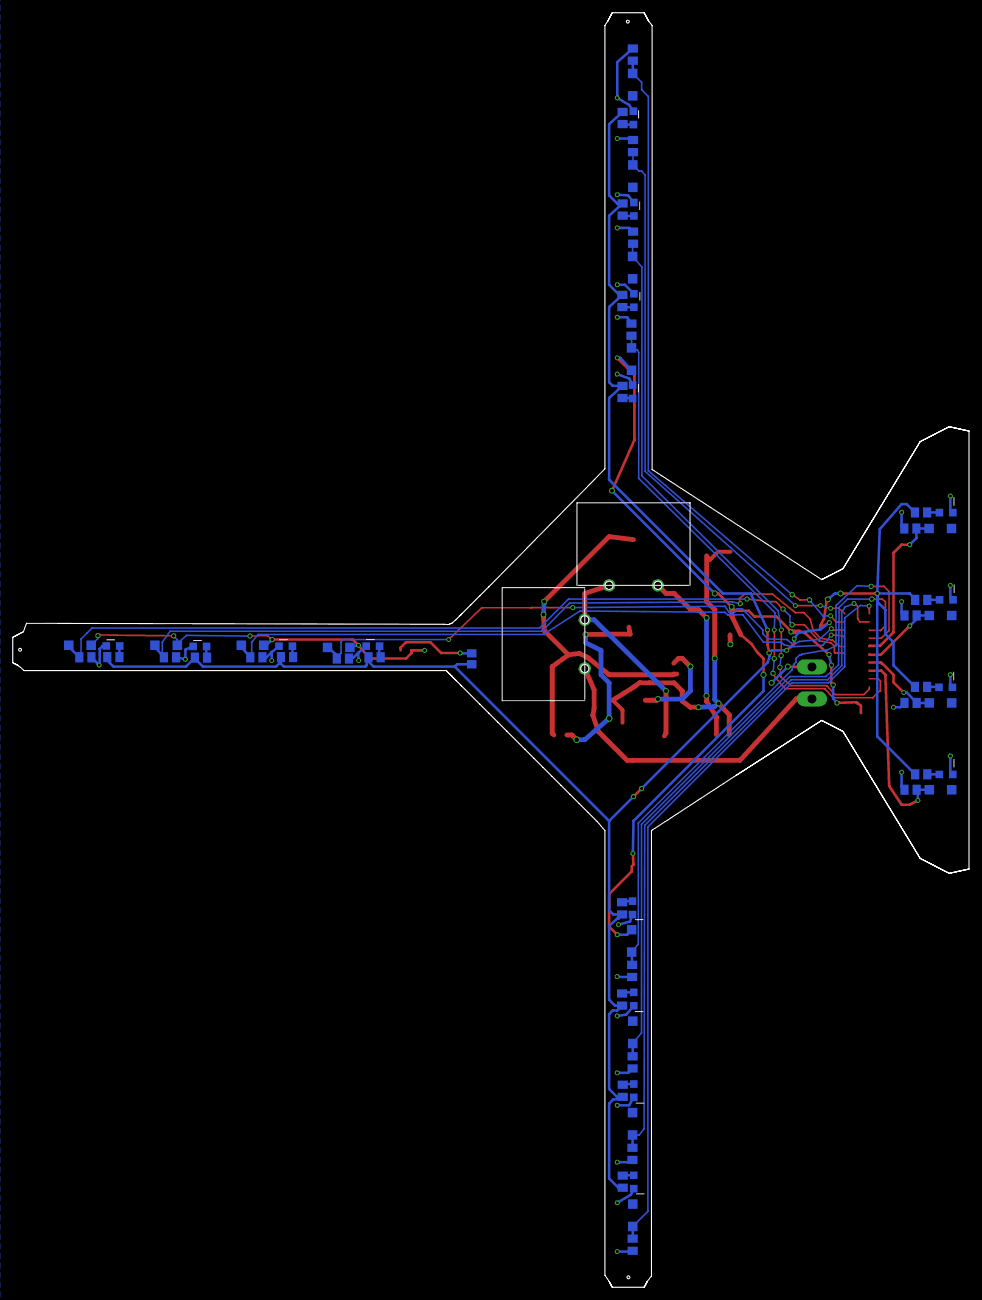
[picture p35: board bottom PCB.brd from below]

Board: 2 copper layers, 149.5 x 199.2 mm, 84 parts (35 on the bottom side), 40 nets.

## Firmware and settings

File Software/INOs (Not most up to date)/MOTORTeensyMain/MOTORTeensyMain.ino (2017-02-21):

//Coded with <3 by Thomas Fraser
#include <t3spi.h>
#include <Light.h>
#include <Motor.h>
#include <Compass.h>
#include <Wire.h>
#include <Math.h>
//#include <SHFCOMMON.h>

T3SPI MOTOR_SLAVE;

Compass compass;

#define dataLength 1

#define COMPASS_ADDRESS 0x68

#define SPI_COUNTER_MAX 2

#define angToRad 0.01745329251
#define radToAng 57.2957795131

volatile uint16_t dataIn[dataLength] = {};

long previousTime;
double heading;

int bestSensor = 0;
int pixyMove = 0;
//int orbit[21] = {0, 1, 1, 1, 7, 9, 10, 11, 12, 13, 14, 7, 8, 9, 10, 12, 11, 13, 15, 1, 1}; //Orbit around ball
//int orbit[21] = {0, 1, 1, 4, 6, 7, 8, 9, 10, 11, 12, 9, 6, 7, 8, 10, 9, 11, 13, 15, 1}; //Experimental Orbit
int orbit[21] = {0,1,2,3,4,5,6,7,8,9,10,11,12,13,14,15,16,17,18,19,20}; //Move Directly to Ball

int lightSensors[16] = {A6, A7, A8, A9, A13, A12, A11, A10, A17, A17 /*This should be A16 but its broken so we will just use A17 instead.*/, A15, A14, A0, A1, A2, A3};
int thresholds[16] = {};

light lightArray = light(A6, A7, A8, A9, A13, A12, A11, A10, A17, A17 /*This should be A16 but its broken so we will just use A17 instead.*/, A15, A14, A0, A1, A2, A3, true); //Left Right Back Front 4 of each
//light lightArray = light(A9, A8, A7, A6, A10, A11, A12, A13, A14, A15, A16, A17, A0, A1, A2, A3);

int moveArray[21][4] = {
    {0,0,0,0},
    {-255, -208, 208, 255},
    {-174, -232, 118, 255},
    {-104, -253, 40, 255},
    {-27, -255, -40, 236},
    {60, -255, -130, 213},
    {180, -255, -255, 180},
    {213, -130, -255, 60},
    {236, -40, -255, -27},
    {255, 40, -253, -104},
    {255, 118, -232, -174},
    {255, 208, -208, -255},
    {174, 232, -118, -255},
    {104, 253, -40, -255},
    {27, 255, 40, -236},
    {-60, 255, 130, -213},
    {-180, 255, 255, -180},
    {-213, 130, 255, -60},
    {-236, 40, 255, 27},
    {-255, -40, 253, 104},
    {-255, -118, 232, 174}
};

Motor motorD(6, 24, 25, 33, 0, 1); //PWM, IN1, IN2, SB, Ignore, Rev
Motor motorA(5, 8, 9, 32, 0, 1);
Motor motorB(3, 0, 1, 30, 0, 1);
Motor motorC(4, 2, 7, 31, 0, 1);

void setup(){
    Wire.begin();
    pinMode(13, OUTPUT);
    Serial.begin(9600);
    MOTOR_SLAVE.begin_SLAVE(ALT_SCK, MOSI, MISO, CS0);
    MOTOR_SLAVE.setCTAR_SLAVE(16, SPI_MODE0);

    NVIC_ENABLE_IRQ(IRQ_SPI0);
    delay(2000);
    digitalWrite(13, HIGH);
    previousTime = micros();
    calcLightReadings(true);
}

void loop(){
    calcLightReadings(true);
    compassData();
    Motor(bestSensor);
    //MotorMove(bestSensor, angle);
    //Serial.println(bestSensor);
}

void spi0_isr(void){ //Wake up in the morning... TRIGGERED [The SPI]
    MOTOR_SLAVE.rx16(dataIn, dataLength);
    bestSensor = dataIn[0];
}

// void MotorMove(int row, int angleIn){
//     int angle = angleIn;
//     motorA.set(int(moveOnAngle(angle, heading, 0))); //Not including Light
//     motorB.set(int(moveOnAngle(angle, heading, 1)));
//     motorC.set(int(moveOnAngle(angle, heading, 2)));
//     motorD.set(int(moveOnAngle(angle, heading, 3)));
// }

void Motor(int row) {
    //float lightSensahs = lightArray.warning45(bestSensor, thresholds);
    //Serial.println(lightSensahs);
    motorA.set(int(moveArray[orbit[row]][0]) + compass.calcHeading(heading)); //* lightSensahs); //Needs Light
    motorB.set(int(moveArray[orbit[row]][1]) + compass.calcHeading(heading)); //* lightSensahs); //Needs Light
    motorC.set(int(moveArray[orbit[row]][2]) + compass.calcHeading(heading)); //* lightSensahs); //Needs Light
    motorD.set(int(moveArray[orbit[row]][3]) + compass.calcHeading(heading)); //* lightSensahs); //Needs Light
}

void compassData(){
    double reading = (double)compass.calcGyro().z;
    long currentTime = micros();
    heading += (((double)(currentTime - previousTime) / 1000000.0) * reading);
    heading = compass.doubleMod(heading, 360.0);
    previousTime = currentTime;
}

int calcCompass_Pixy(){
    if(compass.calcHeading(heading) >= 225 || compass.calcHeading(heading) <= 135){
        return compass.calcHeading(heading);
    }
    else{
        if(pixyMove != 0){
            return pixyMove;
        }
    }
}

int moveOnAngle(int in1, int in3, int in2){ //angle, headingToMove, motor (set motor to -1 if you want a motor speed of 0)
    int angle = in1;
    int headingToMove = in3;
    int motor = in2;

    int speed = 255;
    int angleArray[4] = {60, 135, 225, 300};

    double returnValues[4] = {};
        returnValues[0] = cos(((angleArray[0] + 90) * angToRad) - (angle * angToRad));
        returnValues[1] = cos(((angleArray[1] + 90) * angToRad) - (angle * angToRad));
        returnValues[2] = cos(((angleArray[2] + 90) * angToRad) - (angle * angToRad));
        returnValues[3] = cos(((angleArray[3] + 90) * angToRad) - (angle * angToRad));

    int angleRad = angle * angToRad;

    double modifiedSpeed = speed / doubleAbs(max(max(max(doubleAbs(returnValues[0]), doubleAbs(returnValues[1])), doubleAbs(returnValues[2])), doubleAbs(returnValues[3])));

    int motor_a_val = (int)(returnValues[0] * modifiedSpeed) + compass.calcHeading(headingToMove);
    int motor_b_val = (int)(returnValues[1] * modifiedSpeed) + compass.calcHeading(headingToMove);
    int motor_c_val = (int)(returnValues[2] * modifiedSpeed) + compass.calcHeading(headingToMove);
    int motor_d_val = (int)(returnValues[3] * modifiedSpeed) + compass.calcHeading(headingToMove);

    switch(motor){
        case -1: return 0; break;
        case 0: return (motor_a_val); break;
        case 1: return (motor_b_val); break;
        case 2: return (motor_c_val); break;
        case 3: return (motor_d_val); break;
    }
}

double doubleAbs(double value) {
    if (value > 0) {
        return value;
    } else {
        return -value;
    }
}

void calcLightReadings(bool doIt){
    bool doLight = doIt;
    int lightReadings[16] = {};
    if(doLight == true){
        //calc Light readings
        for(int i = 0; i < 16; i++){
            lightReadings[i] += analogRead(lightSensors[i]);
            thresholds[i] = lightReadings[i] + 30;
        }
        Serial.println("Done Light Calibration :)");
        for(int i = 0; i < 16; i++){
            Serial.println(lightReadings[i]);
        }
        delay(1000);
    }
    else{
    }
}

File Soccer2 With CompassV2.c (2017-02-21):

#pragma config(Sensor, S1,     FIR,            sensorI2CCustom)
#pragma config(Sensor, S2,     BIR,            sensorI2CCustom)
#pragma config(Sensor, S3,     compass,        sensorI2CHiTechnicCompass)
#pragma config(Sensor, S4,     light,          sensorLightActive)
#include "drivers\tris10-findball.h"           !!*//

int ADJRNG = 7;
int ADJSPD = 80;
int COMPRelative;
int COMPCompare;
int str;

task main()
{
	wait10Msec(10);
  	const int COMPOrigin = SensorRaw[S3];
	while(true){
		COMPRelative = SensorValue[S3];
		COMPCompare = COMPOrigin - COMPRelative;
		nxtDisplayTextLine(1, "%i",COMPOrigin,);
		nxtDisplayTextLine(2, "%i",COMPRelative,);
		nxtDisplayTextLine(3, "%i",COMPCompare,);

		if(COMPCompare != -ADJRNG - ADJRNG){
			nxtDisplayTextLine(4, "FIRST IF");
				if((T10FBreadStrength(FIR) + 1) > T10FBreadStrength(BIR)){
					nxtDisplayTextLine(5, "Second IF");
	    			while (T10FBreadStrength(FIR) < 100){
						nxtDisplayTextLine(6, "Can't See");
						COMPRelative = SensorValue[S3];
						COMPCompare = COMPOrigin - COMPRelative;
						nxtDisplayTextLine(1, "%i",COMPOrigin,);
						nxtDisplayTextLine(2, "%i",COMPRelative,);
						nxtDisplayTextLine(3, "%i",COMPCompare,);
						str = T10FBreadStrength(FIR);
						nxtDisplayTextLine(8, "%i",str,);

  						motor[motorA] = 0;
						motor[motorA] = 100;
						motor[motorB] = 0;				//Back
						motor[motorB] = 72;
						motor[motorC] = 0;
						motor[motorC] = 0;
						if(COMPCompare != -ADJRNG - ADJRNG) {
							break;
						}
					}
					while(T10FBreadDir(FIR) == 5){
	    				nxtDisplayTextLine(6, "WHILE5");
						COMPRelative = SensorValue[S3];
						COMPCompare = COMPOrigin - COMPRelative;
						nxtDisplayTextLine(1, "%i",COMPOrigin,);
						nxtDisplayTextLine(2, "%i",COMPRelative,);
						nxtDisplayTextLine(3, "%i",COMPCompare,);
						str = T10FBreadStrength(FIR);
						nxtDisplayTextLine(8, "%i",str,);
	  					motor[motorA] = 0;
						motor[motorA] = 100;
						motor[motorB] = 0;				//Back
						motor[motorB] = 72;
						motor[motorC] = 0;
						motor[motorC] = 0;
						wait1Msec(100);
	    			}

	    			while (T10FBreadDir(FIR) == 4){
	    			    nxtDisplayTextLine(6, "WHILE2");
						COMPRelative = SensorValue[S3];
						COMPCompare = COMPOrigin - COMPRelative;
						nxtDisplayTextLine(1, "%i",COMPOrigin,);
						nxtDisplayTextLine(2, "%i",COMPRelative,);
						nxtDisplayTextLine(3, "%i",COMPCompare,);
						str = T10FBreadStrength(FIR);
						nxtDisplayTextLine(8, "%i",str,);
						motor[motorA] = 0;
						motor[motorA] = 0;
						motor[motorB] = 0;				//Right
						motor[motorB] = 100;
						motor[motorC] = 0;
						motor[motorC] = -95;
								wait10Msec(20);
						motor[motorA] = 0;
						motor[motorA] = -68;
						motor[motorB] = 0;				//Right
						motor[motorB] = 68;
						motor[motorC] = 0;
						motor[motorC] = -100;
							wait10Msec(5);
					}
					while (T10FBreadDir(FIR) == 3){
						nxtDisplayTextLine(6, "WHILE3");
						COMPRelative = SensorValue[S3];
						COMPCompare = COMPOrigin - COMPRelative;
						nxtDisplayTextLine(1, "%i",COMPOrigin,);
						nxtDisplayTextLine(2, "%i",COMPRelative,);
						nxtDisplayTextLine(3, "%i",COMPCompare,);
						str = T10FBreadStrength(FIR);
						nxtDisplayTextLine(8, "%i",str,);
  						motor[motorA] = 0;
						motor[motorA] = -100;
						motor[motorB] = 0;				//Forwards
						motor[motorB] = -72;
						motor[motorC] = 0;
						motor[motorC] = 0;
						wait1Msec(300);
					}
					while (T10FBreadDir(FIR) == 2){
						nxtDisplayTextLine(6, "WHILE4");
						COMPRelative = SensorValue[S3];
						COMPCompare = COMPOrigin - COMPRelative;
						nxtDisplayTextLine(1, "%i",COMPOrigin,);
						nxtDisplayTextLine(2, "%i",COMPRelative,);
						nxtDisplayTextLine(3, "%i",COMPCompare,);
						str = T10FBreadStrength(FIR);
						nxtDisplayTextLine(8, "%i",str,);
						motor[motorA] = 0;
						motor[motorA] = 100;
						motor[motorB] = 0;				//Left
						motor[motorB] = 0;
						motor[motorC] = 0;
						motor[motorC] = 92;
						wait10Msec(20);
						motor[motorA] = 0;
						motor[motorA] = 68;
						motor[motorB] = 0;				//Left
						motor[motorB] = -68;
						motor[motorC] = 0;
						motor[motorC] = 100;
						wait10Msec(5);
					}
					while (T10FBreadDir(FIR) == 1){
						nxtDisplayTextLine(6, "WHILE5");
						COMPRelative = SensorValue[S3];
						COMPCompare = COMPOrigin - COMPRelative;
						nxtDisplayTextLine(1, "%i",COMPOrigin,);
						nxtDisplayTextLine(2, "%i",COMPRelative,);
						nxtDisplayTextLine(3, "%i",COMPCompare,);
						str = T10FBreadStrength(FIR);
						nxtDisplayTextLine(8, "%i",str,);
					  	motor[motorA] = 0;
						motor[motorA] = 100;
						motor[motorB] = 0;				//Back
						motor[motorB] = 72;
						motor[motorC] = 0;
						motor[motorC] = 0;
						wait1Msec(50);
					}
					while (T10FBreadStrength(BIR) > 100) {
						nxtDisplayCenteredTextLine(6, "Behind");
						COMPRelative = SensorValue[S3];
						COMPCompare = COMPOrigin - COMPRelative;
						nxtDisplayTextLine(1, "%i",COMPOrigin,);
						nxtDisplayTextLine(2, "%i",COMPRelative,);
						nxtDisplayTextLine(3, "%i",COMPCompare,);
						str = T10FBreadStrength(FIR);
						nxtDisplayTextLine(8, "%i",str,);
						motor[motorA] = 0;
						motor[motorA] = 100;
						motor[motorB] = 0;				//Backwards
						motor[motorB] = 95;
						motor[motorC] = 0;
						motor[motorC] = 0;
					}
				}
			}



			else(COMPCompare != -ADJRNG-ADJRNG);{
				while(COMPCompare <= -ADJRNG){
					COMPRelative = SensorValue[S3];
					COMPCompare = COMPOrigin - COMPRelative;
					nxtDisplayTextLine(1, "%i",COMPOrigin,);
					nxtDisplayTextLine(2, "%i",COMPRelative,);
					nxtDisplayTextLine(3, "%i",COMPCompare,);
					motor[motorA] = 0;
					motor[motorA] = ADJSPD;
					motor[motorB] = 0;
					motor[motorB] = -ADJSPD;
					motor[motorC] = 0;
					motor[motorC] = -ADJSPD;
				}
				motor[motorA] = 0;
				motor[motorB] = 0;
				motor[motorC] = 0;

				while(COMPCompare >= ADJRNG){
					COMPRelative = SensorValue[S3];
					COMPCompare = COMPOrigin - COMPRelative;
					nxtDisplayTextLine(1, "%i",COMPOrigin,);
					nxtDisplayTextLine(2, "%i",COMPRelative,);
					nxtDisplayTextLine(3, "%i",COMPCompare,);
					motor[motorA] = 0;
					motor[motorA] = -ADJSPD;
					motor[motorB] = 0;
					motor[motorB] = ADJSPD;
					motor[motorC] = 0;
					motor[motorC] = ADJSPD;
				}
				motor[motorA] = 0;
				motor[motorB] = 0;
				motor[motorC] = 0;
			}
	}
}

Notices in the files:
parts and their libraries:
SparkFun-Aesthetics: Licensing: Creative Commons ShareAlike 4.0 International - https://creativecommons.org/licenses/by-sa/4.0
